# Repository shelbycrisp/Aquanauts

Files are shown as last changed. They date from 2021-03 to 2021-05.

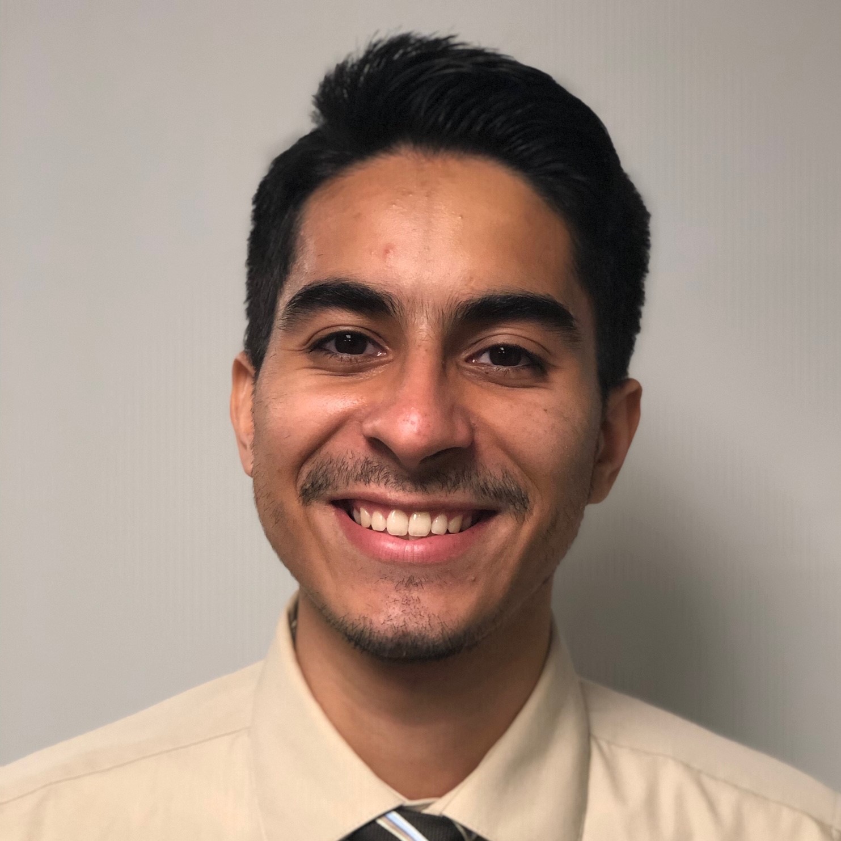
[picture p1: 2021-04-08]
website/ruben-headshot.JPG

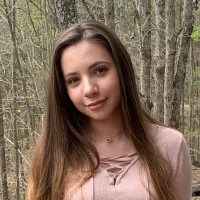
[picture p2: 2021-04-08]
website/shayna-headshot.jpg

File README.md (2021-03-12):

# Aquanauts
## Summary

The Exxon Valdez oil spill of 1989 is generally considered to have the largest environmental impact of any oil spill to date. Ocean Scientists at Prince William Sound have been using an underwater profiler to monitor environmental factors. The platform has an anchor that holds it at a specified depth. The platform goes to the surface of the water once a day to transmit a signal that it is still alive. The data collected on ocean life and ocean currents is not transmitted and must be retrieved by scientists. The collected data gives scientists information on how the location and its inhabitants are recovering. There are multiple ways this platform can be improved and updated. Currently, someone must retrieve the platform every few weeks in order to charge the battery and extract data. Over time the battery life has decreased, further increasing the maintenance required. If this maintenance could be decreased that would be a great improvement for the platform. Currently, it is very difficult and expensive to replace the battery. A battery that can be serviced by the scientists themselves would be ideal. The platform has many sensors on board to detect ocean life such as plankton. The current solution to classifying plankton is through the use of machine learning. However, there is room for improvement in this component. There is a weather buoy nearby that could potentially be used to install components on for communication with the platform. Our team is identifying which features/issues to focus our project on.

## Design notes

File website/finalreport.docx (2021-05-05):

Prince William Sound Profiler

ECE 4873 Senior Design Project

Aquanauts

Dr. Mick West

Dr. Robert Campbell (if applicable)

Shayna Seidel, EE, sseidel7, sseidel7@gatech.edu

Jim O’Donnell, CmpE, jodonnell3, jodonnell3@gatech.edu

Shelby Crisp, CmpE, scrisp3, scrisp3@gatech.edu

Jason Lee, EE, slee3117, slee3117@gatech.edu

Ruben Quiros, CmpE, rquiros6, rquiros6@gatech.edu

Timothy Pierce, EE, tpierce31, timrpierce31@gatech.edu

Table of Contents

Executive Summary …………………………………………………………………... 3

1. Introduction ……………………………………………………………………….. 5
2. Project Description and Goals ……………………………………………………. 7
3. Technical Specification ……………………………………………………………. 9
4. Design Approach and Details …………………………………………………….. 10
  4.1 Design Concept Ideation, Constraints, Alternatives, and Tradeoffs …………. 10
  4.2 Preliminary Concept Selection and Justification …………………………….. 12
  4.3 Engineering Analysis and Experiments …………………………………….... 17
  4.4 Codes and Standards …………………………………………………………. 17
5. Project Demonstration …………………………………………………………….. 19
6. Schedule, Tasks, and Milestones ………………………………………………… 23
7. Marketing and Cost Analysis …………………………………………………….. 25
  7.1 Marketing Analysis …………………………………………………………... 25
  7.2 Cost Analysis …………………………………………………………………. 26
8. Current Status …………………………………………………………………….. 27
9. Leadership Roles ………………………………………………………………….. 28
10. References …………………………………………………………………………. 29

Appendix ……………………………………………………………………………. 31

Executive Summary

The goal of this project was to design a new communications system for an existing underwater profiler. This allows a data-collecting profiler in the Prince William Sound to send the collected data to researchers. The current transfer of information necessitates a biweekly data transfer on site of the profiler, which is 4 hours offshore in the Prince William Sound. With the newly designed communications module, data will be transferred once every 12 hours without the need for onsite download. This module needs to surface and communicate wirelessly to the shore in an environment with few options for long range transfer of data. The profiler currently uses low bandwidth cellular data to send minimal information every 12 hours. The new system should not take up too much battery life, and should include an interface between existing sensors that are necessary to surface in the profiler. The total cost for this project was $354.85.

Nomenclature

AMP: Autonomous Moored Profiler

BOM: Bill of Materials

CmpE: Computer Engineer

EE: Electrical Engineer

PCB: Printed Circuit Board

PWS: Prince William Sound

Prince William Sound Profiler Communication Module

1. Introduction

In the aftermath of the 1989 Exxon Valdez oil spill in Prince William Sound, an Autonomous Moored Profiler (AMP) has been used (since 2013) to collect data on PWS’s environmental recovery [1]. Although originally manufactured by Sea-Bird Scientific, the profiler is no longer in production. The current profiler in PWS continues to monitor the environmental recovery of PWS, but requires numerous updates and improvements. This is why the Aquanauts team created a data transmission system for the profiler in Prince William Sound. This system is able to send data from the profiler sensors to the ocean scientists and give the scientists the flexibility to individually control sensors. This functionality will give scientists more information on a regular basis. The total cost for this project was $354.85.

Currently, scientists must visit the profiler approximately every two weeks to charge the battery and manually collect data. Making frequent maintenance trips to the profiler is inefficient, and can become delayed or even dangerous due to weather conditions. Remote access to sensor data would greatly enhance the profiler's usage. Data transmission would require using the nearby 3G cell tower to transmit data to the ocean scientists so they could access it without making a trip to the profiler.

The current system has all the sensors on a single relay system such that sensors cannot be individually controlled. Certain sensors cannot collect data as the profiler travels downward, so all sensors are off during this time. A new relay system that can control sensors individually would allow more flexibility for data collection and increase the amount of data collected.

This design involved connecting all sensors to the new switching board and a centralized microcontroller, and designing a method for the system to transmit data when at the surface. There were multiple constraints that had to be taken into account for this design. Due to the nature of the profiler, designs must withstand the extreme pressure, temperature, and storms of PWS. The system must also fit inside a 3.937 inch diameter capsule. These requirements were factored into the design. Once the design was complete, a combination of simulations and physical tests were conducted to demonstrate the module’s capabilities. The verification was a video and presentation used at the Spring 2021 Senior Design Expo. The rest of this report will go into greater detail on the specifics of designing and validating this system.

2. Project Description, Customer Requirements, and Goals

The Aquanauts team proposed a new sensor module in addition to the overall profiler assembly to address three of the customer’s main requirements: improved data transfer from the profiler’s remote location, extended battery life of the overall profiler, and updated central data storage. The new module addresses these requirements in the following ways:

1. Revamp the method of communication to improve data transfer volume and speed by utilizing the available 3G/4G cell tower nearby.
2. Provide physical infrastructure and software capability to turn individual sensors on and off on a schedule, thus saving critical battery life.
3. Provide a modern microprocessor and data storage unit for aggregation and processing of data, replacing the outdated and no longer produced Persistor module.

Success and stakeholder acceptance will be measured by benchmarking performance of the new module versus current-state performance. Notably, current-state data transfer is every 10th data point amounting to around 200kb of data, with the majority of communication representing an “alive” signal that indicates whether the profiler is still functioning. Battery life is estimated between 3 weeks and 1 month, with the majority of power drain resulting from the anchoring winch. The project’s internal stakeholder is Dr. West, while the external stakeholder is Dr. Campbell and his team in Alaska.

Table 1. Stakeholder 2x2

Internal Stakeholders | External Stakeholders
Dr. West, Aquanauts | Dr. Campbell

Constraints are minimal. The intent of the long-term project with the research team is to design a new profiler as the existing profiler is no longer manufactured. The Aquanauts’ goal is to provide an ideal sensor and communication subsystem to address the research team’s requirements, rather than consider integration with other existing systems. Considerations include data transfer rate, low power consumption, environmental survivability of the components in terms of temperature and pressure in a very cold underwater environment, and appropriate storage capacity to accommodate profiling data.

Table 2. QFD Chart

| Long-Range Communication | Centralized Data Storage and Processing | Extended Battery Life | Extended Profiling Capability | Total
Form Factor | 2 | 4 | 10 | 10 | 26
Power Consumption | 4 | 4 | 10 | 7 | 25
Environmental Conditions | 10 | 10 | 2 | 2 | 24
Total | 16 | 18 | 22 | 19

3. Technical Specifications

Table 3. Technical Specifications

Specification | Min | Max
Functional Temperature | -5 C | 30 C
Functional Depth | N/A | 60m
Total Power Consumption for Sensors | 12 V DC, 480 mA (** Missing min amp info for SBE 16plus V2) | 12 V DC, 1.1 A (**Missing max amp info for SBE 16plus V2)
Communication Range (Approx) | 8000m (Nearest cell tower, approximately 5 mi.) | N/A
Communication Protocols | 3G, 4G, FTP/SFTP

The specifications listed in Table 3 indicate the foundational requirements of the integrated system, including functional temperature, depth, power consumption, communication range, and communication frequency. All defined sections are equally important as they encompass environmental considerations for the remote underwater locale, power consumption considerations in terms of saving critical battery life, and communications requirements for improved data transfer. The minimum power consumption is determined from the highest minimum operating voltage of all sensors, and maximum power consumption is determined from the lowest maximum operating voltage of all sensors. Minimum communication range is an approximation based on the operating depth of the profiler to a theoretical buoy containing additional communication equipment, and maximum communication range is from the profiler’s location to the nearest cell tower 5 miles (~8000 meters) away. 3G and 4G are the fastest available communication protocols using the nearby cellular tower.

4. Design Approach and Details
  4.1 Design Concept Ideation, Constraints, Alternatives, and Tradeoffs

The current design concept for this project is to have a central processor which will interface between the different sensors used by the profiler. The processor will store sensor data in a central place as well as interface with a cellular communication module to send the data out while profiling.

4.1.1 Power Switching Functionality

In order to have the capability to control individual sensors, a power switching system needed to be designed. The system currently used in PWS has all the sensors on a single relay so they are all turned on and off together. To control sensors separately, they must each have their own power switch.

Using optocouplers for each sensor was initially considered, but no optocouplers with a high enough current rating and low enough price were found. Next, solid state relays were considered for their long term reliability, but similarly to the high current optocouplers, solid state relays are expensive. Finally, MOSFETs were considered because all of the sensors use DC power. MOSFETs were chosen for their ease of implementation as well as their low price. Each sensor has a corresponding MOSFET that when conducting, connects the ground lead of the sensor to ground and allows the sensor to receive the necessary voltage and draw the needed current.

Table 4. Switching Board Tradeoffs

Tradeoffs for Power Switching Board
Pros | - Individual control of sensors
Cons | - A new board had to be designed - Components for board had to be purchased

4.1.2 Data Transmission

Data transmission is a main focus for this project. Different concepts were considered, including satellite transmission for data, cellular telemetry and radio transmission. Cellular data is what is currently utilized for transmitting information from the profiler to shore. Using cellular data made the most sense for application of this project. Since cellular data was already being utilized, it was more ideal for use in testing as opposed to radio transmission and satellite transmission. There is a cellular tower near the sound that can support 3G/4G communications.

While cellular data is useful to utilize, the constraint of inability to send data without surfacing still comes into play. Satellites would require a buoy and therefore a signal would persist even under harsher conditions. However, upon further inspection, satellites were beyond the budget of this project and not many companies support satellite communication at such a remote location. Viasat, one of the larger and more affordable companies to offer satellite transmission, doesn’t immediately offer transmission to the sound [2]. Radio transmission is another option to explore, but would require testing and setup in the sound that would have been hard to reproduce offsite.

Table 5. Cellular Data Tradeoffs

Tradeoffs for Cellular data usage
Pros | - In use currently - Easier to test
Cons | - Doesn’t work if the module doesn’t surface - May have lower speeds than other alternatives

4.1.3 Centralized Sensors

In order to successfully collect and store data as well as control the sensors and communications module, a central processor was necessary. The one already in use, a Persistor, is no longer being produced. Multiple microcontrollers were considered such as Arduino Mega and multiple Raspberry Pi models. Ultimately a Raspberry Pi model 3B was selected. This model of Raspberry Pi uses the least power while offering Linux compatibility to support well-known communication protocols like FTP/SFTP/SCP as well as the Sixfab Cellular Kit.

This PCB and microcontroller must fit inside the capsule and be able to function at low temperatures and high pressure in an underwater environment.

An alternative would be to keep the current processor. Since it is no longer being produced and uses outdated software, it would be close to impossible to test the integration of sensors and communication modules. If any damage were to occur with the current processor, it would be harder to replace than something like an Arduino or Raspberry Pi which are still in production.

Table 6. Updating Central Storage Tradeoffs

Tradeoffs for Updating central storage
Pros | - Old processor no longer in production - Can update software - Compatible with cellular kit
Cons | - Added cost - Old processor still working and in use

  4.2 Preliminary Concept Selection and Justification

4.2.1 Power Switching Functionality

After discussing the power requirements with Dr. West and Dr. Campbell, the Aquanauts decided to design a PCB that allowed for the sensors to be turned on and off individually using MOSFETs. Currently, the profiler lacks individual sensor power control and all sensors must be turned on at the same time. Individual sensor power control will allow the profiler to collect data on its descent. The ability to turn on only the needed sensors will conserve battery life.

The selected power switches for sensor control are FQP30N06L power MOSFETs. These power MOSFETs were chosen for their high power dissipation capabilities and their ease of implementation. The chosen MOSFETs are capable of dissipating 79W of power which far exceeds the power draw of any of the onboard sensors. The maximum power draw of any of the individual sensors is 11.25W which is low enough to not require the use of heat sinks on the MOSFETs.

To convert the voltage to usable DC levels for both the sensors and the Raspberry Pi, two DC-DC Buck converters were used to buck the voltage from the onboard 30V 1.5kWHr battery. All four sensors currently on the profiler have voltage ranges that include 12V so this was the selected voltage for conversion. A Mean Well 18-36V to 12V power converter was used that is capable of outputting 30W - significantly more than the maximum power draw of all four sensors. To buck the voltage to usable levels for the Raspberry Pi, a Traco Power 12W, 5.1V output buck converter was used.

There are currently four sensors on the profiler, but a total of six MOSFET switches were added to allow more sensors to be added in the future. To control the MOSFETs, a separate GPIO pin from the Raspberry Pi was connected to the gate of each MOSFET. The GPIO pin from the Raspberry Pi was set to 3.3V to trigger the MOSFET and supply the connected sensor with 12V. To protect the sensors in case of a voltage or current spike, a fuse specified for the power requirements of each sensor was added.

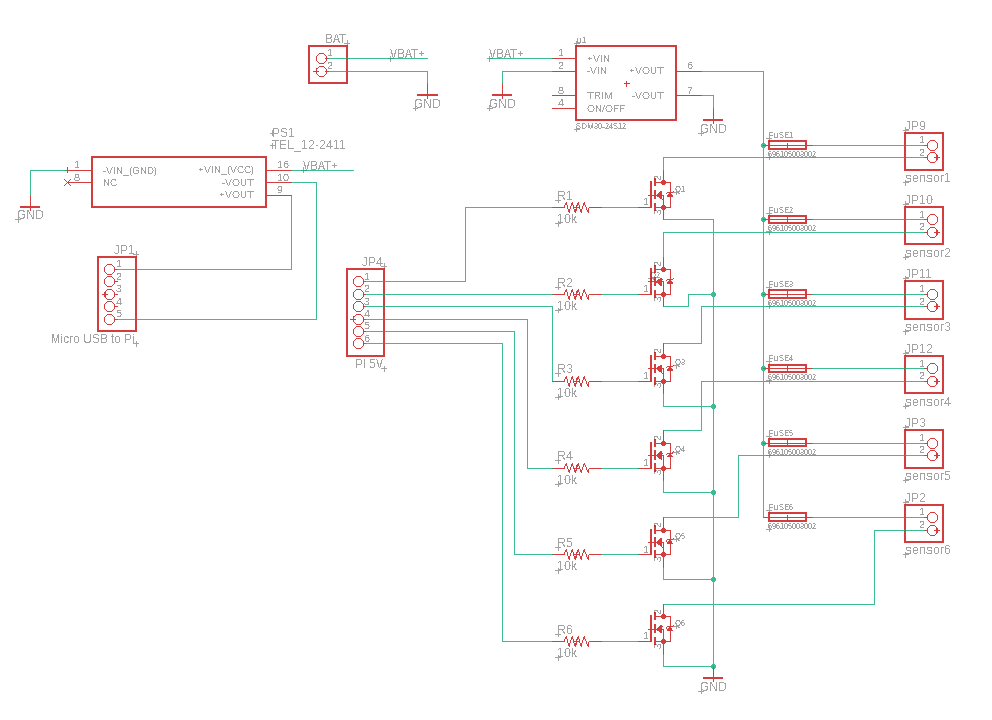
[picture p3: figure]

Figure 1. Eagle schematic showing the layout for the MOSFET sensor switching board

Once the schematic was completed, the PCB was designed with several constraints in mind. Each trace on the PCB is rated for 2.5A which is greater than the highest current draw of a sensor by more than a factor of 1.5. The PCB was also designed to fit in a vacuum sealed tube suitable for keeping electronics dry under water. The diameter of the tube is 100mm or 3.937in and the dimensions of the PCB are 3.5 inches by 3.9 inches. When creating the layout of the PCB, thermal and ease of use considerations were taken into account. The components that generate the most heat, the DC-DC converters and the MOSFETs, were spaced out as much as possible while also keeping the PCB within size constraints. Additionally, the MOSFET, fuse, resistor, and pin header for each individual sensor were grouped together in order to make identifying blown fuses and their corresponding sensor easier.

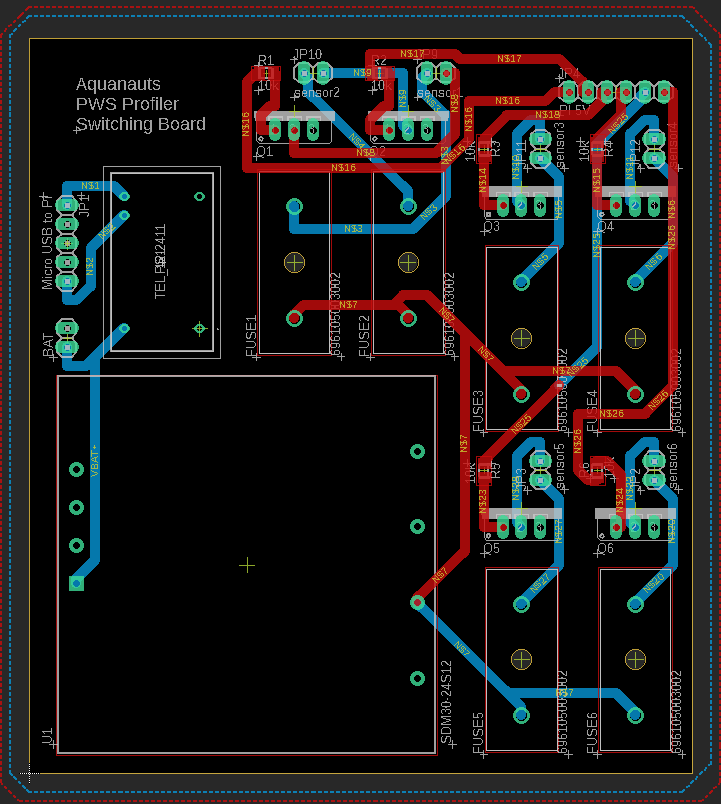
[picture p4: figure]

Figure 2. The final MOSFET sensor switching board PCB layout. The dimensions of the board are 3.9 inches (from top to bottom) by 3.5 inches (from left to right)

4.2.2 Centralized Sensors

Currently, data from the sensors is stored in a central location using ASCII text. The main storage unit is a Persistor which is outdated and no longer produced. A new microcontroller must be chosen to accommodate the sensors on the module, cellular data transmission, expandable memory, and ease of programming. The sensors the microcontroller needs to interface with are: SBE 49 FastCAT CTD Sensor, RBR Brevio, Seabird Eco FLNTU, SBE 63 Optical Dissolved Oxygen Sensor, Aanderaa Oxygen Optode, and Seabird SUNA V2 Nitrate Sensor. A Raspberry Pi 3B was used to replace the Persistor. This was best suited for this project because it has many pins to accommodate the sensors, expandable pin modules can be added if needed, and there are multiple kits already developed for using cell data with a Raspberry Pi. Raspberry Pi’s run using a limited version of Ubuntu. This would give our team easy access to a multitude of preexisting data transmission commands. The Pi 3B can run these commands without the excessive power draw of the Pi 4.

4.2.3 Data Transmission

When the module is at the surface, data from the sensors will be transmitted. Currently when the profiler surfaces, a nearby 3G cell tower is used to send minimal information. Due to availability and cost, the Aquanauts plan is to continue to use this cell tower for the increased data transmission. The Aquanauts have selected the Sixfab 4G LTE Cell Hat. This kit is specifically designed to interface with 4G cellular towers which are currently being utilized in the sound. This kit is comprehensive, which was an attractive feature for our team in testing, but in the future a more whittled down version could be used. While 5G was considered, the 4G cellular tower was just installed in the Prince William Sound, and the likelihood that 4G would become obsolete any time soon is unlikely.

  4.3 Engineering Analyses and Experiment

The Aquanauts team performed simulations for both hardware and software for experiments on our design. The three Computer Engineers were tasked with simulating the system in software, with programs and libraries that operate on the final product. When the three Electrical Engineers designed and fabricated the PCB, they were in charge of performing tests on the hardware to make sure it could safely operate under the required power conditions. Power consumption was monitored to determine how much power the overall module would consume.

In the following phase, the software and hardware teams were able to test the overall system. The team performed experiments to make sure that the processing unit was able to send data through the new communication system. This involved the use of real data that Dr. Campbell has collected. Unfortunately, the team did not have access to neither the battery nor the sensors. As a result, a 2 W resistor was used to simulate the sensor, and a DC power supply was used to simulate the battery. This proved that the current electronics worked with a new communication system and a centralized data processing unit.

  4.4 Codes and Standards

The relevant codes and standards include the following:

- IMT-2000: Offers the capability of providing value-added services and applications for frequencies between 400 MHz and 3 GHz [6].
  - Adds compatibility feature with existing systems such as 2G
  - Makes 3G systems affordable
- 802.15.4-2020 - IEEE Standard for Low-Rate Wireless Networks: The standard provides for ultra low complexity, ultra low cost, ultra low power consumption, and low data rate wireless connectivity among inexpensive devices, especially targeting the communications requirements of what is now commonly referred to as the Internet of Things [7].
5. Project Demonstration

To validate the specifications of the Prince William Sound Profiler communication system and sensor switching board, a series of both software and hardware tests were performed. Testing the communication system used the Raspberry Pi 3b, the Raspberry Pi cellular kit, the Samsung Evo SSD, and the custom printed circuit board. A DC-DC buck converter on the PCB was used to lower the battery-level voltages to 5.1V to power the Raspberry Pi. The Raspberry Pi was connected to the PCB, and the SSD and Sixfab cellular kit were connected to the Raspberry Pi. Using a remote FTP server hosted off campus, the communication module was tested by executing a shell script on the Raspberry Pi, which sent sample data files to the FTP server through a wireless connection.

For the validation of the sensor switching system on the custom PCB, both software simulations and hardware tests were performed. First, a single MOSFET switching circuit was simulated using LTSpice to verify that the chosen design could power the sensor by providing 12V and then turn off the sensor by providing 0V. To simulate the sensor, a 75Ω, 2W resistor was used to draw a current of about 160mA.

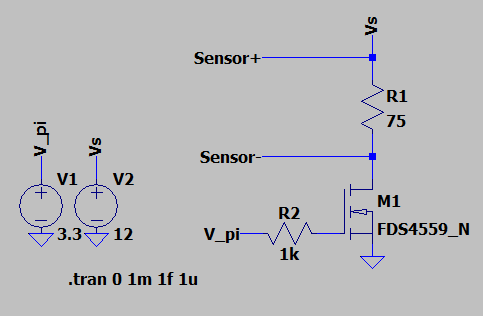
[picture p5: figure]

Figure 3. LTSpice schematic for a single MOSFET sensor switch when the Raspberry Pi sends a 3.3V signal to turn the sensor on

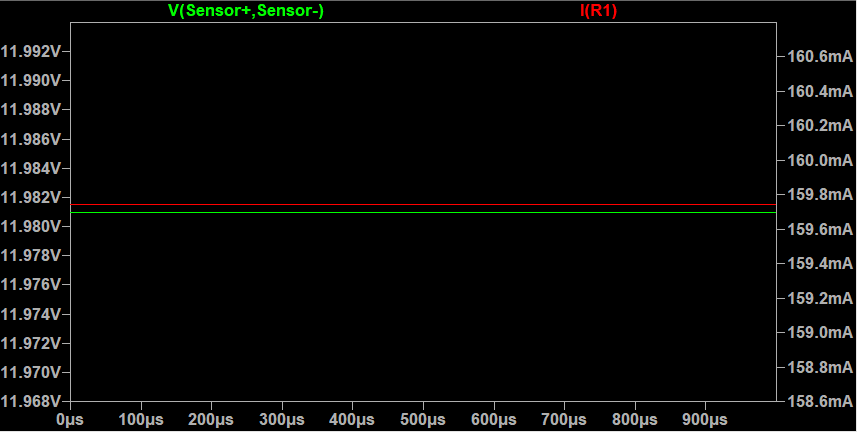
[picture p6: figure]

Figure 4. LTSpice transient simulation results showing 12V and 160mA being supplied to the 75Ω resistor simulating a sensor

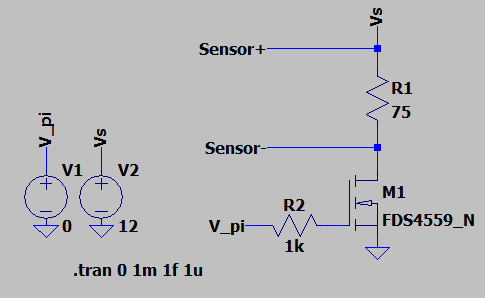
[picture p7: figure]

Figure 5. LTSpice schematic for a single MOSFET sensor switch when the Raspberry Pi sends a 0V signal to turn the sensor off

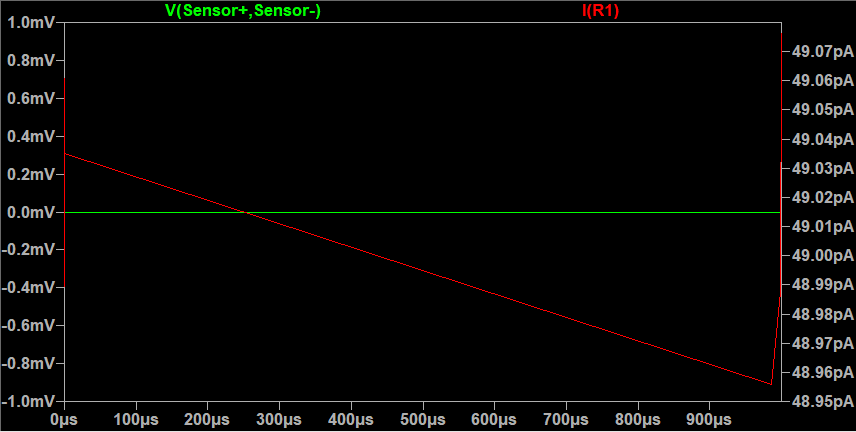
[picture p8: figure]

Figure 6. LTSpice transient simulation results showing 0V and nearly 0mA being supplied to the 75Ω resistor simulating a sensor

Once the custom PCB with the sensor switching system was complete, hardware tests were performed to verify that the switching system worked as intended. The Raspberry Pi was hooked up to the PCB and a 75Ω, 2W resistor was wired to the output of the MOSFET switching system. The voltage across the resistor and the current through the resistor were measured using a digital multimeter. When the Raspberry Pi supplied 3.3V to the gate of the MOSFET, the voltage across the resistor was 12V and the current through the resistor was 160mA. When the Raspberry Pi supplied 0V to the gate of the MOSFET, the voltage across the resistor was reduced to 0V and the current across the resistor was reduced to 0mA, effectively turning the “sensor” off.

When the design aspect of the project was complete, results were prepared and presented at the Spring 2021 Senior Design Capstone Expo. A poster was created to show an overview of the system that was designed, and a project video was created to present motivations for this project and demonstrate the system.

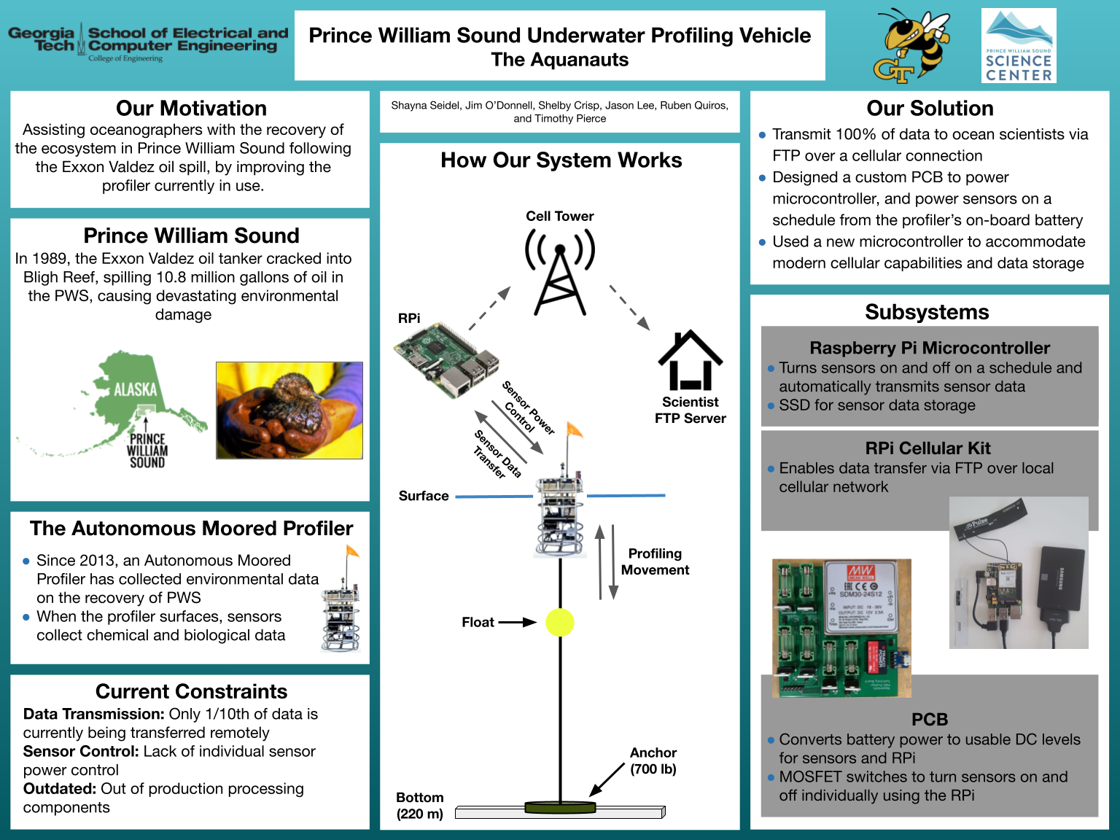
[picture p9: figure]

Figure 7. Senior Design Capstone Expo Poster with background information of the project and an overview of the designed system

6. Schedule, Tasks, and Milestones:

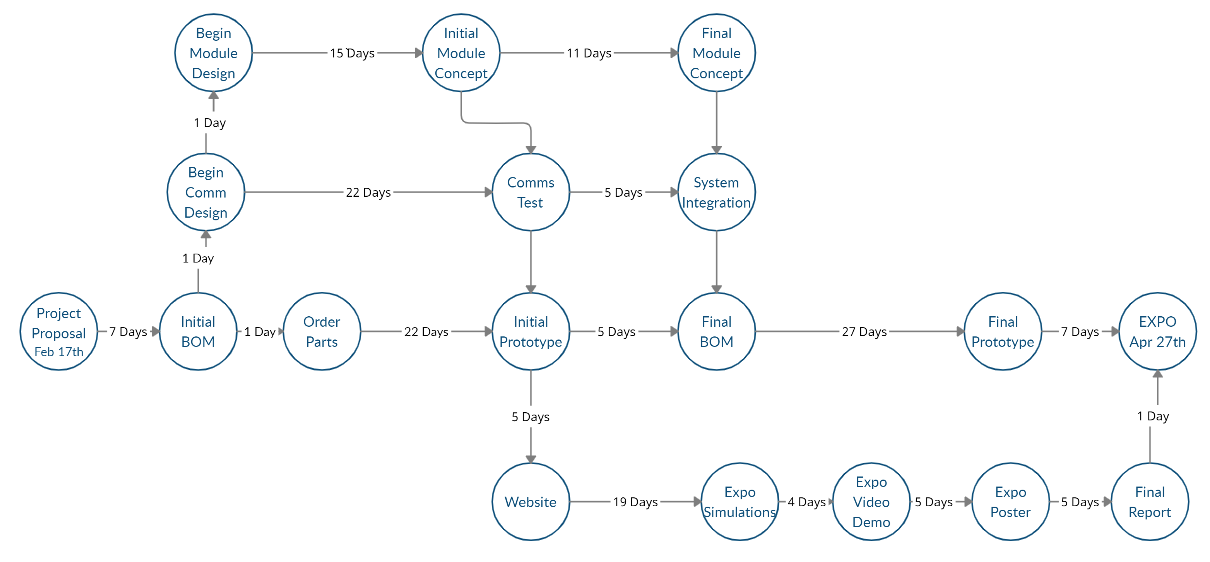
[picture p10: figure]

Figure 8. PERT Chart showing the expected timeline for module development

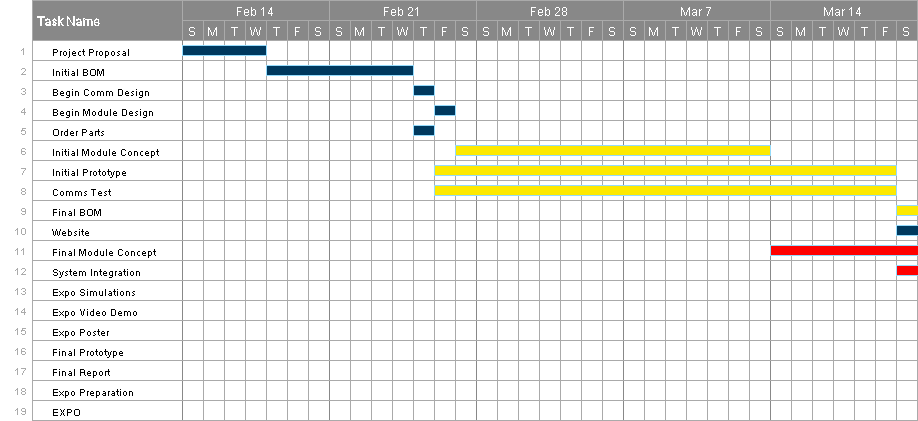
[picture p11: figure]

Figure 9. Gantt chart for February 14th to March 20th showing a timeline of project phases and their estimated difficulty. Purple indicates low difficulty, yellow indicates medium difficulty, and red indicates high difficulty.

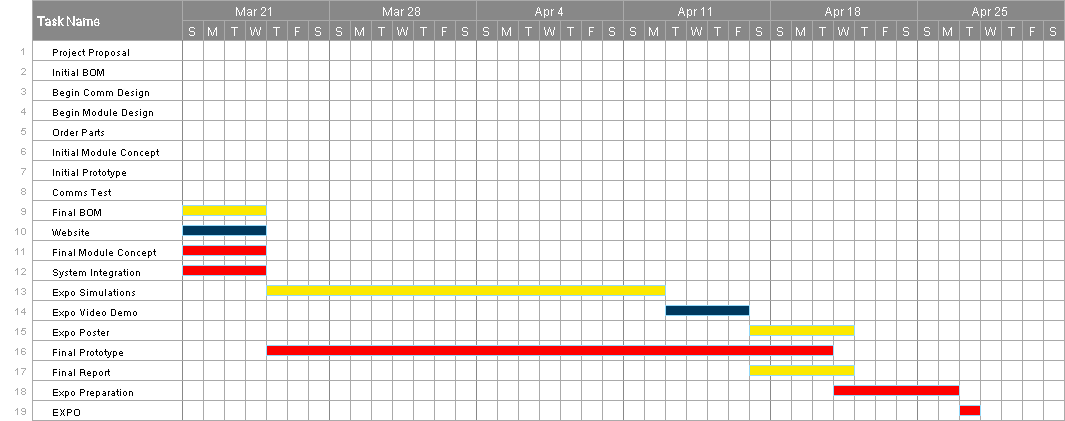
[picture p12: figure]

Figure 10. Gantt chart for March 21st to April 27th showing a timeline of project phases and their estimated difficulty. Purple indicates low difficulty, yellow indicates medium difficulty, and red indicates high difficulty.

At the start of the project, the chance of successful project completion by April 27th was determined to be 95%. The project utilized pre existing technology and did not rely on any significant technological breakthroughs. The completion of the project did not directly follow the outlined timeline in the PERT chart and Gantt charts. Much more time was dedicated to initial product research and design. Because more time was devoted to designing the system for this project, less time was needed for the final prototype and integration of the system. Additionally, significantly less time was needed for expo preparation. After a successful Senior Design Capstone Expo, the goal was met and the project was officially completed by the deadline.

7. Marketing and Cost Analysis
  7.1 Marketing Analysis

The proposed communication module is a newly designed long range wireless communication unit that will be an addition to a Sea Bird Thetis profiler currently deployed in the Prince William Sound. What is currently in use for external communications is an RS-232 100 Mbps serial to IP ethernet device. This sends a signal when the profiler itself surfaces.

There are some products that boast wireless communications without the necessity to leave the water. DSPComm has a line of underwater acoustic modems [8]. They are manufactured to be used underwater and can transmit a signal up to 3km away. Our product does not need to have such a long underwater range, as it can surface to transmit.

Another similar product on the market is the MarineLabs CoastScout. This long range communication buoy is a self-contained and self-powered buoy that is capable of transmitting 5MB wirelessly. The CoastScout is its own data collection device that collects weather and water data and sends it to a remote server. Our device differs from the CoastScout because instead of collecting its own data and sending it, it will be sending data that was collected by the underwater Thetis profiler. Additionally, the communication module will rely on power from the Thetis profiler battery instead of solar power.

  7.2 Cost Analysis

Table 7. Costs

Part | Manufacturer | Retailer | Price per Item | Quantity | Part Total
Raspberry Pi 3B | Raspberry Pi | Amazon | 37.99 | 1 | 37.99
Raspberry Pi 4G/LTE Cellular Modem Kit | Sixfab | Sixfab | 109 | 1 | 109
Sixfab Connect Sim | Sixfab | Sixfab | 2 | 1 | 2
SAMSUNG PRO Plus SDHC Full Size SD Card 32GB | Samsung | Amazon | 9.99 | 1 | 9.99
MKR SD PROTO SHIELD | Arduino | Arduino | 13.8 | 1 | 13.8
USB 3.0 SATA III Hard Drive Adapter Cable, SATA to USB Adapter Cable | SKL Tech | Amazon | 7.99 | 1 | 7.99
SAMSUNG 870 EVO 250GB 2.5 Inch SATA III Internal SSD | Samsung | Amazon | 39.99 | 1 | 39.99
30 W DC/DC Converter | Mean Well USA | Digi-Key | 26.71 | 1 | 26.71
FQP30N06L | ON Semiconductor | Digi-Key | 1.22 | 6 | 7.32
USB to Serial RS232 Adapter | SIIG | Amazon | 49.85 | 1 | 49.85
12 W DC/DC Converter | Traco Power | Digi-Key | 28 | 1 | 28
PCB | JLC PCB | JLC PCB | 14.8 | 1 | 14.8
500 mA Fuse | Bel Fuse Inc | Digi-Key | 0.234 | 5 | 1.17
1A Fuse | Bel Fuse Inc | Digi-Key | 0.224 | 5 | 1.12
5x20 mm Fuse Holder | Würth Elektronik | Digi-Key | 0.64 | 8 | 5.12

Total

354.85

8. Current Status

The overall task of this project was to create a new communication system for the underwater profiler, which will be a major upgrade to the original system. Sub-tasks are listed below:

a. Designing a subsystem that collects data from all sensors on the profiler - COMPLETE
  i. Design and manufacture a PCB to control sensors individually and power the microcontroller - COMPLETE
b. Designing a subsystem that will send the data to the research facility over a wireless connection - NEARLY COMPLETE
  i. Testing the ability to send files over WiFi - COMPLETE
  ii. Testing the ability to send files over a cellular connection - INCOMPLETE.
- Due to time constraints at the end of the semester and troubleshooting issues, we were unable to complete testing of the AT command set with our cellular HAT. We have included as much information as we were able to gather, and the process is detailed nearly in full in the User Manual. This would be a good place for a future team to continue research and testing.
c. Create a full BOM - COMPLETE
  i. Order parts - COMPLETE
d. Project proposal and presentation - COMPLETE
9. Leadership Roles
a. Group Leader: Jim O’Donnell
- Main speaker and scheduling coordinator
b. Expo Coordinator: Shayna Seidel
- In charge of making sure the team is aware of all requirements for the expo
c. Financial Advisor: Seungju Jason Lee
- Responsible for keeping track of receipts and handling reimbursements
d. Webmaster: Ruben Quiros
- Responsible for managing the team’s website
e. Documentation Coordinator: Timothy Pierce
- In charge of maintaining and submitting documentation on behalf of the group
f. Tech lead: Shelby Crisp
- Host and manager of the git repository
10. References
1. R. W. Campbell, P. L. Roberts, and J. Jaffe, “Prince William Sound Plankton Camera: a profiling in situ observatory of plankton and particulates,” OUP Academic, 24-Mar-2020. [Online]. Available: https://academic.oup.com/icesjms/article/77/4/1440/5811106. [Accessed: 17-Feb-2021].
2. Admin, “How it Works: The technology behind satellite internet,” Viasat.com. [Online]. Available: https://www.viasat.com/about/newsroom/blog/how-it-works-the-technology-behind-satellite-internet/. [Accessed: 18-Feb-2021].
3. S.-B. S. USA, “Thetis Autonomous Moored Profiler Datasheet,” Sea-Bird Scientific. [Online]. Available: https://www.seabird.com/systems/thetis-profiler/family-downloads?productCategoryId=54627869948. [Accessed: 17-Feb-2021].
4. ARDUINO SIM - MKR GSM 1400 Cellular Kit. [Online]. Available: https://store.arduino.cc/usa/sim-bundle. [Accessed: 17-Feb-2021].
5. H. H. A. K. A. www.crazyhamster.co.uk, IP Ratings Explained - know your enclosure Ingress Protection ratings. [Online]. Available: https://www.enclosurecompany.com/ip-ratings-explained.php. [Accessed: 17-Feb-2021].`
6. “About mobile technology and IMT-2000,” International Telecommunication Union. [Online]. Available: https://www.itu.int/osg/spu/imt-2000/technology.html. [Accessed: 17-Feb-2021].
7. “802.15.4-2020 - IEEE Standard for Low-Rate Wireless Networks,” IEEE Xplore. [Online]. Available: https://ieeexplore.ieee.org/document/9144691/metrics#metrics. [Accessed: 18-Feb-2021].
8. “Products,” Underwater Wireless Modem and Communication Devices, 05-Feb-2021. [Online]. Available: http://www.dspcommgen2.com/products/. [Accessed: 18-Feb-2021].
9. Xylem, Aanderaa Oxygen Optode 4531. Xylem, Bergen, Norway, 2020. Datasheet. https://www.aanderaa.com/productsdetail.php?Oxygen-Optodes-2
10. Xylem, Aanderaa Oxygen Optode 4835. Xylem, Bergen, Norway, 2020. Datasheet. https://www.aanderaa.com/productsdetail.php?Oxygen-Optodes-2
11. RBR, RBRBrevio C.T.D. RBR, Ottawa, Ontario, 2019. Datasheet. https://rbr-global.com/products/standard-loggers/rbrbrevio
12. Seabird, ECO FLbb Fluorometer and Scattering Meter. Seabird, Bellevue, WA, 2021. Datasheet. https://www.seabird.com/combination-sensors/eco-flntu/family?productCategoryId=54758054352
13. Seabird, SBE 49 FastCAT CTD Sensor. Seabird, Bellevue, WA, 2015. Datasheet. https://www.seabird.com/profiling/sbe-49-fastcat-ctd-sensor/family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
14. Seabird, SBE 63 Optical Dissolved Oxygen Sensor. Seabird, Bellevue, WA, 2014. Datasheet. https://www.seabird.com/oxygen-sensors/sbe-63-optical-dissolved-oxygen-sensor/family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
15. Seabird, SUNA V2 UV Nitrate Sensor. Seabird, Bellevue, WA, 2017. Datasheet. https://www.seabird.com/nutrient-sensors/suna-v2-nitrate-sensor/family?productCategoryId=54627869922

Appendix

Sensors | Min Voltage | Max Voltage | Min Current (mA) | Max Current (mA)
SBE 16plus V2 | 9 | 28 | N/A | N/A
SBE 43 | 6.5 | 24 | 2.5 | 9.23
SUNA Nitrate Sensor | 8 | 18 | 416.67 | 937.5
Echo Fluorometer | 7 | 15 | 60 | 140

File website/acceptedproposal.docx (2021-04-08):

Prince William Sound Profiler Communication Module

ECE 4873 Senior Design Project

Aquanauts

Dr. Mick West

Dr. Robert Campbell (if applicable)

Shayna Seidel, EE, sseidel7, sseidel7@gatech.edu

Jim O’Donnell, CmpE, jodonnell3, jodonnell3@gatech.edu

Shelby Crisp, CmpE, scrisp3, scrisp3@gatech.edu

Jason Lee, EE, slee3117, slee3117@gatech.edu

Ruben Quiros, CmpE, rquiros6, rquiros6@gatech.edu

Timothy Pierce, EE, tpierce31, timrpierce31@gatech.edu

Submitted

2/17/21

Table of Contents

Executive Summary 3

1. Introduction ……………………………………………………………………….. 5
2. Project Description and Goals ……………………………………………………. 7
3. Technical Specification ……………………………………………………………. 9
4. Design Approach and Details …………………………………………………….. 10
  4.1 Design Approach ……………………………………………………………... 10
  4.2 Codes and Standards …………………………………………………………. 15
5. Project Demonstration …………………………………………………………….. 17
6. Schedule, Tasks, and Milestones ………………………………………………… 18
7. Marketing and Cost Analysis …………………………………………………….. 20
  7.1 Marketing Analysis …………………………………………………………... 20
  7.2 Cost Analysis …………………………………………………………………. 20
8. Current Status …………………………………………………………………….. 22
9. Leadership Roles ………………………………………………………………….. 23
10. References …………………………………………………………………………. 24

Appendix ……………………………………………………………………………. 26

Executive Summary

The goal of this project is to design a new communications module for an existing underwater profiler. This module will be able to send data from a data-collecting profiler in the Prince William Sound to the researchers working on it. The current transfer of information necessitates a biweekly data transfer on site of the profiler, which is 4 hours offshore in the Prince William Sound. By designing a new communications module, data will be transferred once every 24 hours without the need for onsite download. This module will need to surface in the sound and communicate wirelessly to shore in an environment with few options for long range transfer of data. The profiler currently uses low bandwidth cellular data to send minimal information every 24 hours. The added module shouldn’t take up too much battery life, and should include an interface between existing sensors that are necessary to surface in the profiler. The expected cost is $183.78.

Nomenclature

AMP: Autonomous Moored Profiler

BOM: Bill of Materials

CmpE: Computer Engineer

EE: Electrical Engineer

PWS: Prince William Sound

Prince William Sound Profiler Communication Module

1. Introduction

In the aftermath of the 1989 Exxon Valdez oil spill in Prince William Sound, an Autonomous Moored Profiler (AMP) has been used (since 2013) to collect data on PWS’s environmental recovery [1]. Although originally manufactured by Sea-Bird Scientific, the profiler is no longer available. The current profiler in PWS continues to monitor the environmental recovery of PWS but requires numerous updates and improvements. This is why the Aquanauts team is requesting $400 of funding to create a data transmission module for a profiler in Prince William Sound. This module will be able to surface and send data from the profiler sensors to the ocean scientists. This functionality will save energy thus reducing the maintenance frequency while giving scientists more information on a regular basis. The current cost estimate for parts for this module is $183.78, however, the total project will cost more when PCB printing and components that are unaccounted for are taken into account.

Currently, scientists must visit the profiler approximately every two weeks to charge the battery. These maintenance visits are when data from the sensors is collected. Making frequent maintenance trips to the profiler is inefficient, and can become delayed or even dangerous due to weather conditions. Saving battery life and accessing sensor data remotely would greatly enhance the profiler's usage. Developing a smaller module to surface, as opposed to the entire large platform, would save battery life and decrease maintenance visits. This module would also use the nearby 3G cell tower to transmit data to the ocean scientists so they could access it without making a trip to the profiler.

This module will require a separate smaller winch to ascend to the surface. However, the Aquanaut’s focus is on the module itself and mainly its software and electrical hardware components. This will involve connecting all sensors to the module and a centralized microcontroller, and designing a method for the module to transmit data when at the surface. There are multiple constraints that must be taken into account for this design. Due to the nature of the profiler, designs must withstand the water, pressure, temperature, and harsh storms of PWS. These requirements will be factored into the design. Once design is complete, a combination of simulations and physical tests will be conducted to demonstrate the module’s capabilities. The verification will be videos for use at the Spring 2021 Senior Design Expo. The rest of this report will go into greater detail on the specifics of designing and validating this module.

2. Project Description, Customer Requirements, and Goals

The Aquanauts team proposes a new sensor module in addition to the overall profiler assembly to address four of the customer’s main requirements: improved data transfer from the profiler’s remote location, extended battery life of the overall profiler, updated central data storage, and extended profiling capabilities. The new module will address these requirements in the following ways:

1. Revamp the method of communication to improve data transfer volume and speed by offering a higher baud rate than the existing 9600 baud, and utilize the available 3G cell tower nearby.
2. Use a smaller integrated winch to release the sensor module to the water’s surface when broadcasting data, thus saving critical battery life by eliminating the need to surface the full profiler on a daily basis via the anchoring winch.
3. Relocate the full array of sensors to a smaller and less invasive module. This will allow the potential for profiling in both the up and down directions of movement. Currently, the profiler does not collect data while moving downward to prevent profiling water that has washed through the large 6 ft. by 2 ft. profiler assembly. This “washed-through” water is not representative of the environment around the profiler.
4. Provide a modern data storage unit and processor for aggregation of data, replacing the outdated and no longer produced Persistor module.

Success and stakeholder acceptance will be measured by benchmarking performance of the new module versus current-state performance. Notably, current-state data transfer is every 10th data point amounting to around 200kb of data with the majority of communication representing an “alive” signal that indicates whether the profiler is still functioning. Battery life is estimated between 3 weeks and 1 month, with the majority of power drain resulting from the anchoring winch. The project’s internal stakeholder is Dr. West, while the external stakeholder is Dr. Campbell and his team in Alaska.

Table 1. Stakeholder 2x2

Internal Stakeholders | External Stakeholders
Dr. West, Aquanauts | Dr. Campbell

Constraints are minimal. The intent of the long-term project with the research team is to design a new profiler as the existing profiler is no longer manufactured. The Aquanauts goal is to provide an ideal sensor and communication subsystem to address the research team’s requirements, rather than consider integration with other existing systems. Considerations will include data transfer rate, low power consumption, environmental survivability of the components in terms of temperature and pressure in a very cold underwater environment, and appropriate storage capacity to accommodate profiling data.

Table 2. QFD Chart

| Long-Range Communication | Centralized Data Storage and Processing | Extended Battery Life | Extended Profiling Capability | Total
Form Factor | 2 | 4 | 10 | 10 | 26
Power Consumption | 4 | 4 | 10 | 7 | 25
Environmental Conditions | 10 | 10 | 2 | 2 | 24
Total | 16 | 18 | 22 | 19

3. Technical Specifications

Table 3. Technical Specifications

Specification | Min | Max
Functional Temperature | -5 C | 30 C
Functional Depth | N/A | 100m
Total Power Consumption | 9 Vdc, 1.01 A (** Missing min amp info for RBR Brevio) | 14 Vdc, 1.67 A (**Missing max amp info for RBR Brevio)
Communication Range (Approx) | 100m (Operating depth + realistic estimate of surface buoy distance) | 8000m (Nearest cell tower, approximately 5 mi.)
Communication Frequency | GSM 850 MHz for remote 3G compatibility (869.2 – 893.8 MHz) Other available frequencies: E-GSM 1900 MHz, DCS 1800 MHz, PCS 1900 MHz

The specifications listed in Table 3 indicate the foundational requirements of the integrated system, including functional temperature, depth, power consumption, communication range, and communication frequency. All defined sections are equally important as they encompass environmental considerations for the underwater and highly remote locale, power consumption considerations in terms of saving critical battery life, and communications requirements for improved data transfer. The minimum power consumption is determined from the highest minimum operating voltage of all sensors, and maximum power consumption is determined from the lowest maximum operating voltage of all sensors. Minimum communication range is an approximation based on the operating depth of the profiler to a theoretical buoy containing additional communication equipment, and maximum communication range is from the profiler’s location to the nearest cell tower 5 miles (~8000 meters) away. The communication frequency, GSM 850 MHz, is the standard frequency used in data transfer to 3G cell towers.

4. Design Approach and Details
  4.1 Design Concept Ideation, Constraints, Alternatives, and Tradeoffs

The current design concept for this project is to have a central processor which will interface between the different sensors used by the profiler. The processor will store sensor data in a central place as well as interface with a cellular communication module to send the data out while profiling.

4.1.1 Smaller module

The current Prince William Sound profiler completely surfaces through the use of a winch. The winch is the greatest power draw and necessitates a large battery. One concept to conserve energy is to utilize a smaller module that surfaces to profile without surfacing with the battery. Through the use of a second winch, the large battery can remain at a lower depth, only needing to surface for charging. Since a smaller winch is used, less power will be expended. This smaller module will need to house the profiling sensors as well as a module for data transmission.

A constraint of a smaller module is the ability for it to withstand strong currents and storm conditions in the sound. The current profiler is sometimes overtaken by currents and is unable to surface and therefore cannot send a signal to indicate that it’s still working. When this occurs, the profiler needs to be checked on, which is a dangerous task especially under storm conditions. The sturdiness and surfacing abilities of the smaller module must be taken into account. If the separation of a smaller module from the profiler causes more issues when it comes to surfacing, the benefits of having a smaller module will be negated.

A few alternatives to the smaller module would be keeping the design as is and losing power saving capabilities, or having a buoy sitting at the surface to transmit messages. With the use of a buoy, the profiler would be able to stay submerged and use the buoy as a relay point for information. This would solve the problem of currents keeping the profiler from surfacing and allow for seamless communications with the shore. The buoy itself could have a solar powered battery so it doesn’t draw additional power from the profiler and therefore will not need to be serviced frequently. We decided against the use of a buoy because of the short lifespan previous buoys have had when utilized in the Prince William Sound. Previous buoys used by Dr. Campbell in the Prince William sound have only lasted around three weeks due to high boat traffic as well as strong weather conditions. Having to replace the buoy on a monthly basis would negate the benefits of using a buoy.

Table 4. Smaller Module Tradeoffs

Tradeoffs for Smaller module use
Pros | - Less power used - Safer than buoy use
Cons | - Added complexity - May not surface properly - no signal sent

4.1.2 Data Transmission

A data transmission module is a main focus for this project. Different concepts were considered, including satellite transmission for data, cellular telemetry and radio transmission. Cellular data is what is currently utilized for transmitting information from the profiler to shore. Using cellular data will make the most sense for application of this project. Since cellular data is currently utilized, it will be more ideal for use in testing as opposed to radio transmission and satellite transmission. There is a cellular tower near the sound that can support 3G communications.

While cellular data is useful to utilize, the constraint of inability to send data without surfacing still comes into play. Satellites would require a buoy and therefore a signal would persist even under harsher conditions. However, upon further inspection, satellites would be beyond the budget of this project and not many companies support satellite communication at such a remote location. Viasat, one of the larger and more affordable companies to offer satellite transmission, doesn’t immediately offer transmission to the sound [2]. Radio transmission is another option to explore, but would require testing and setup in the sound that would be hard to reproduce offsite.

Table 5. Cellular Data Tradeoffs

Tradeoffs for Cellular data usage
Pros | - In use currently - Easier to test
Cons | - Doesn’t work if the module doesn’t surface - May have lower speeds than other alternatives

4.1.3 Centralized Sensors

In order to successfully collect and store data as well as control the sensors and communications module, a central processor will be necessary. While there is one currently in use, it is no longer being produced. The plan for this project is to replace the old processor with one that is newer and can run a lightweight version of ubuntu in order to interface with some of the sensors.

One constraint to keep in mind are the conditions that this electronic component will be working under. The processor will be functioning at low temperatures and high pressure in an underwater environment. Special care needs to be taken to keep it in a waterproof enclosure and make sure any wiring or exposed pieces are protected.

An alternative would be to keep the current processor. Since it is no longer being produced and uses outdated software, it would be close to impossible to test the integration of sensors and communication modules. If any damage were to occur with the current processor, it would be harder to replace than something like an arduino or raspberry pi which are still in production.

Table 6. Updating Central Storage Tradeoffs

Tradeoffs for Updating central storage
Pros | - Old processor no longer in production - Can update software
Cons | - Added cost - Old processor still working and in use

  4.2 Preliminary Concept Selection and Justification

4.2.1 Smaller Module to Save Battery Life

After reviewing documentation and discussing the AMP needs with Dr. West and Dr. Campbell, the Aquanauts decided to design a module to ascend to the surface. One motivation for this was saving battery life. The profiler is rather large (diameter: 78.75 cm, length 212cm) [3] and uses much of the battery life to visit the surface. Since profiling occurs while travelling up the water column to the surface, this module must house the sensors needed for profiling. The module itself will need to be waterproof and sealed adequately to protect the electronics inside. The module will require a smaller winch to send the module to the surface and then back to the AMP. The module will also need to be connected to the power supply (currently the battery). This can be accomplished using a long cable with adequate protection/sleeving. The Aquanauts focus is moreso on the technology that will go inside this module and less on the mechanical aspects of this module.

4.2.2 Centralized Sensors

Currently, data from the sensors is stored in a central location using ASCII text. The main storage unit is a Persistor which is outdated and no longer produced. A new microcontroller must be chosen to accommodate the sensors on the module, cellular data transmission, expandable memory, and ease of programming. The sensors the microcontroller needs to interface with are: SBE 49 FastCAT CTD Sensor, RBR Brevio, Seabird Eco FLNTU, SBE 63 Optical Dissolved Oxygen Sensor, Aanderaa Oxygen Optode, and Seabird SUNA V2 Nitrate Sensor. The current plan is to use an Arduino Mega. This is best suited for this project because it has many pins to accommodate the sensors, expandable pin modules can be added if needed, there are multiple kits already developed for using cell data with Arduino, Arduino uses a C style language, and several Aquanauts have prior experience with Arduino. If an error occurs that makes the Arduino Mega no longer viable for the necessary functions, there are other models of Arduino and other microcontrollers such as Raspberry Pi that would be researched as replacements.

4.2.3 Data Transmission

When the module is at the surface, data from the sensors will be transmitted. Currently when the profiler surfaces, a nearby 3G cell tower is used to send minimal information. Due to availability and cost, the Aquanauts plan is to continue to use this cell tower for the increased data transmission. If this method ends up not being viable, there are backup methods such as satellite that can be further explored. The Aquanauts have selected the Arduino GSM 1400 Cellular Kit [4]. This kit is specifically designed to use the GSM/3G network which this module will be using. There are multiple attachments that can be used with an Arduino for cell data connection if there are issues with this kit.

  4.3 Engineering Analyses and Experiment

The Aquanauts team will perform simulations for both hardware and software for experiments on our design. The three Computer Engineers will be tasked with simulating the system in software, with programs and libraries that will operate on the final product. Once the three Electrical Engineers have designed the PCB, they will be in charge of performing tests on the hardware to make sure it will safely operate under certain power conditions. Power consumption can be monitored to determine how much power this module will be consuming. This is an important step as power should be saved using a smaller module.

In the next phase, the software and hardware teams will be able to test the overall system. In other words, we will perform experiments to make sure that the processing unit is able to send data through the new communication system. This will involve the use of real data that Dr. Campbell has collected. The Aquanauts will also ideally have access to real sensors which can be connected and used to simulate how the current profiling system works. This will prove that the current electronics will work with a new communication system and a centralized data processing unit.

  4.4 Codes and Standards

The relevant codes and standards include the following:

- IP69K: The IP (Ingress Protection) Code is an international standard that rates a product’s protection against intrusions by water and foreign particles. The 6 represents solid particle protection and the 9K represents the moisture protection. IP69K is rated as "dust tight" and protected against complete, continuous submersion in water [5].
  - The new modules that we introduce must be able to operate in continuous submersion.
- The Research Vessel Safety Standards (RVSS) appendix states that the tension in the rope must be monitored at the operator’s station with a resolution of a certain frequency depending on the factor of safety [6].
  - The rope of the winch must be able to meet the tension requirements with the addition of new modules.

802.15.4-2020 - IEEE Standard for Low-Rate Wireless Networks: The standard provides for ultra low complexity, ultra low cost, ultra low power consumption, and low data rate wireless connectivity among inexpensive devices, especially targeting the communications requirements of what is now commonly referred to as the Internet of Things [7].

5. Project Demonstration

To validate the specifications of the Prince William Sound Profiler Communication Module, a combination of software simulations, demonstration video, and a physical prototype with available components used to model the profiler will be used. Additionally, remote communication tests will be performed and software simulations will be used to validate the communication abilities of the communication module.

For the virtual senior design expo, the project demonstration will include the following: simulation results presented in a descriptive manner with important data highlighted to show that requirements have been met, a scaled down prototype of the profiler communication module to show how the system works, and video to provide demonstrations that can not be performed during the expo.

6. Schedule, Tasks, and Milestones:


Figure 1. PERT Chart showing the expected timeline for module development


Figure 2. Gantt chart for February 14th to March 20th showing a timeline of project phases and their estimated difficulty. Purple indicates low difficulty, yellow indicates medium difficulty, and red indicates high difficulty.


Figure 3. Gantt chart for March 21st to April 27th showing a timeline of project phases and their estimated difficulty. Purple indicates low difficulty, yellow indicates medium difficulty, and red indicates high difficulty.

The PWS profiler communication module will take advantage of pre-existing technology to upgrade a well documented profiler. Because our team is using established technology, our chance of success is not reliant on technological breakthroughs. The factor that has the largest chance of preventing success is falling behind schedule and hitting unexpected roadblocks. With the PERT chart and the Gantt chart establishing a timeline for the project, these roadblocks will be minimized. Considering the above factors, the team’s chance of finishing the project a week before the expo is 95%.

7. Marketing and Cost Analysis
  7.1 Marketing Analysis

The proposed communication module will be a newly designed long range wireless communication unit that will be an addition to a Sea Bird Thetis profiler currently deployed in the Prince William Sound. What is currently in use for external communications is an RS-232 100 Mbps serial to IP ethernet device. This sends a signal when the profiler itself surfaces.

There are some products that boast wireless communications without the necessity to leave the water. DSPComm has a line of underwater acoustic modems [8]. They are manufactured to be used underwater and can transmit a signal up to 3km away. Our product will not need to have such a long underwater range, as it can surface to transmit.

Another similar product on the market is the MarineLabs CoastScout. This long range communication buoy is a self-contained and self-powered buoy that is capable of transmitting 5MB wirelessly. The CoastScout is its own data collection device that collects weather and water data and sends it to a remote server. Our device differs from the CoastScout because instead of collecting its own data and sending it, it will be sending data that was collected by the underwater Thetis profiler. Additionally, the communication module will rely on power from the Thetis profiler battery instead of solar power.

  7.2 Cost Analysis

Currently, the group spends approximately three hours a week for meetings. These meetings are held to discuss the current status and the future goals of the project. Half of these meetings are held with our supervisor, Dr. West. This opportunity allows the group to receive feedback and produce an improved approach to the goal. Although the group works on reports and other documents during the meeting, some members may spend up to an additional hour adding to the report. Once the goals and the scope of the project have been solidified, each member will spend approximately eight hours a week to complete the tasks that were assigned. This time will still include the times spent for the meetings and the report documentation, but it will also be composed of times used to design the new components that the group aims to produce.

Table 7. Expected Costs

Part | Quantity | Manufacturer | Retailer | Price per Item | Total
Arduino Mega 2560 | 1 | Arduino | Arduino | $40.30 | $40.30
Arduino SIm MKR GSM 1400 Cellular Kit | 1 | Arduino | Newegg | $119.69 | $119.69
PRO Plus SD Card 32GB | 1 | Samsung | Amazon | $9.99 | $9.99
MKR SD Proto Shield | 1 | Arduino | Arduino | $13.80 | $13.80

8. Current Status

As of the time of submission of this proposal, it is estimated that the Aquanauts have completed about 20 percent of their project. Up to this point, the Aquanauts have a general design idea, but have not built anything yet. The design process will take place in the next phase.

The overall task of this project is to create a new communication system for the underwater profiler, which will be a major upgrade to the original system. Sub-tasks are listed below:

a. Designing a new centralized storage for all of the data in the profiler - IN PROGRESS
b. Designing a system that will send the data to the research facility over a cellular connection - IN PROGRESS
c. Designing software programs for the two components listed above - INCOMPLETE
d. Create a full BOM - IN PROGRESS
  i. Order parts - INCOMPLETE
e. Project proposal and presentation - IN PROGRESS
9. Leadership Roles
a. Group Leader: Jim O’Donnell
- Main speaker and scheduling coordinator
b. Expo Coordinator: Shayna Seidel
- In charge of making sure the team is aware of all requirements for the expo
c. Financial Advisor: Seungju Jason Lee
- Responsible for keeping track of receipts and handling reimbursements
d. Webmaster: Ruben Quiros
- Responsible for managing the team’s website
e. Documentation Coordinator: Timothy Pierce
- In charge of maintaining and submitting documentation on behalf of the group
f. Tech lead: Shelby Crisp
- Host and manager of the git repository
10. References
1. R. W. Campbell, P. L. Roberts, and J. Jaffe, “Prince William Sound Plankton Camera: a profiling in situ observatory of plankton and particulates,” OUP Academic, 24-Mar-2020. [Online]. Available: https://academic.oup.com/icesjms/article/77/4/1440/5811106. [Accessed: 17-Feb-2021].
2. Admin, “How it Works: The technology behind satellite internet,” Viasat.com. [Online]. Available: https://www.viasat.com/about/newsroom/blog/how-it-works-the-technology-behind-satellite-internet/. [Accessed: 18-Feb-2021].
3. S.-B. S. USA, “Thetis Autonomous Moored Profiler Datasheet,” Sea-Bird Scientific. [Online]. Available: https://www.seabird.com/systems/thetis-profiler/family-downloads?productCategoryId=54627869948. [Accessed: 17-Feb-2021].
4. ARDUINO SIM - MKR GSM 1400 Cellular Kit. [Online]. Available: https://store.arduino.cc/usa/sim-bundle. [Accessed: 17-Feb-2021].
5. H. H. A. K. A. www.crazyhamster.co.uk, IP Ratings Explained - know your enclosure Ingress Protection ratings. [Online]. Available: https://www.enclosurecompany.com/ip-ratings-explained.php. [Accessed: 17-Feb-2021].`
6. “Winch and wire regulations,” Scripps Institution of Oceanography. [Online]. Available: https://scripps.ucsd.edu/ships/planning/winch-and-wire. [Accessed: 17-Feb-2021].
7. “802.15.4-2020 - IEEE Standard for Low-Rate Wireless Networks,” IEEE Xplore. [Online]. Available: https://ieeexplore.ieee.org/document/9144691/metrics#metrics. [Accessed: 18-Feb-2021].
8. “Products,” Underwater Wireless Modem and Communication Devices, 05-Feb-2021. [Online]. Available: http://www.dspcommgen2.com/products/. [Accessed: 18-Feb-2021].
9. Xylem, Aanderaa Oxygen Optode 4531. Xylem, Bergen, Norway, 2020. Datasheet. https://www.aanderaa.com/productsdetail.php?Oxygen-Optodes-2
10. Xylem, Aanderaa Oxygen Optode 4835. Xylem, Bergen, Norway, 2020. Datasheet. https://www.aanderaa.com/productsdetail.php?Oxygen-Optodes-2
11. RBR, RBRBrevio C.T.D. RBR, Ottawa, Ontario, 2019. Datasheet. https://rbr-global.com/products/standard-loggers/rbrbrevio
12. Seabird, ECO FLbb Fluorometer and Scattering Meter. Seabird, Bellevue, WA, 2021. Datasheet. https://www.seabird.com/combination-sensors/eco-flntu/family?productCategoryId=54758054352
13. Seabird, SBE 49 FastCAT CTD Sensor. Seabird, Bellevue, WA, 2015. Datasheet. https://www.seabird.com/profiling/sbe-49-fastcat-ctd-sensor/family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
14. Seabird, SBE 63 Optical Dissolved Oxygen Sensor. Seabird, Bellevue, WA, 2014. Datasheet. https://www.seabird.com/oxygen-sensors/sbe-63-optical-dissolved-oxygen-sensor/family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
15. Seabird, SUNA V2 UV Nitrate Sensor. Seabird, Bellevue, WA, 2017. Datasheet. https://www.seabird.com/nutrient-sensors/suna-v2-nitrate-sensor/family?productCategoryId=54627869922

Appendix

Sensor | Min Voltage | Max Voltage | Min Amps | Max Amps | Min Temp | Max Temp | Max Depth | Notes
Aandera Optode 4531 (RS-232) | 5 Vdc | 30 Vdc | 0.16 mA + 40 mA/S | 100mA | -5 C | 30 C | 100m | RS-232 output format
Aandera Optode 4531 (Analog) | 7 Vdc | 30 Vdc | 0.16 mA + 40 mA/S | 100mA | -5 C | 30 C | 100m | Analog output format
Aandera Optode 4835 | 5 Vdc | 14 Vdc | 0.16 mA + 48 mA/S | 100mA | -5 C | 40 C | 300m | RS-232 output format
RBR Brevio | 4.5 V | 30 V | ??? | ??? | -5 C | 35 C | 750m (Plastic), 6000m (Titanium) | RS-232 output format
Searbird ECO FLbb Fluorometer | 7 Vdc | 15 Vdc | 140 µA | 60 mA | ??? | ??? | 600m | RS-232 output format, 19200 baud
Seabird SBE 49 FastCAT CTD Sensor | 9 Vdc | 24 Vdc | 350 mA (9V), 285 mA (12V), 180 mA (19V) | 750 mA (Turn-on transient) | -5 C | 35 C | 350m (Plastic), 7000m (Titanium) | RS-232 output format
Seabird SBE 63 Dissolved Oxygen Sensor | 6 Vdc | 24 Vdc | 35 mA | 35 mA | 0 C | 30 C | 600m (Plastic), 7000m (Titanium) | RS-232 output format
Seabird SUNA V2 UV Nitrate Sensor | 8 Vdc | 18 Vdc | 625 mA (12V) | 625 mA (12V) | 0 C | 35 C | 500m | Serial data output, assuming RS-232
**mA/S is milliamps per sampling interval in seconds | | | Total min amps (mA) | Total max amps (mA) | Overall Min Temp | Overall Max Temp | Overall Max Depth
| | | 1010.62 | 1670 | 0 C | 30 C | 100m

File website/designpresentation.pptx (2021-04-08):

## Prince William Sound Profiler Mid-semester Design Review

ECE 4873 Senior Design Project
Aquanauts

## Introduction

- 1989 Exxon Valdez oil spill caused environmental damage
- Since 2013 an autonomous moored profiler (AMP) has collected data on PWS recovery
- Profiler needs modifications/updates
- Goals:
- Updated data storage and transmission capabilities for existing profiler
  - Module can send data from profiler sensors to scientists
  - Centralized data storage in module
- Relay system to supply power to sensors on-demand

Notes: Shayna

## Project Description and Goals

- Customer Requirements
  - Higher data transfer volume and speed
  - Updated central memory and processing
  - Automated system to turn sensors on/off on a schedule
- How we will address each
  - Revamp communications utilizing the nearby 3G/4G cell tower and updated data transfer rates vs. current 2G utilization
  - Direct FTP of data will provide full data transfer vs. the current direct UDP packetized transfer only representing 1/10th of collected data
  - Updated memory and processing unit to replace outdated/no longer manufactured Persistor
    - Raspberry Pi 3B
    - Samsung 870 EVO Solid State Drive
  - Custom-built MOSFET switching board to supply power to on-board sensors on a schedule
    - Conserves battery life

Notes: jim

## Technical Specification

Table 3. Technical Specifications

Specification | Min | Max
Functional Temperature | -5 C | 30 C
Functional Depth | Sea level | 60m
Total Power Consumption | 9 Vdc, 1.01 A | 14 Vdc, 1.67 A
Communication Range (Approx) | 8000m (Nearest cell tower, approx. 5 miles) | N/A
Communication Protocol | 3G & 4G SFTP (Direct to local server, or to cloud)

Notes: Jim

## Design Approach and Details

- Update Processor
  - Raspberry Pi 3B
    - Choice considerations:
      - Lowest power consumption of RPi models that support Linux
      - Linux required for ftp & ssh protocols
      - Arduino does not support Linux
      - USB bootable from SSD
    - Cons
      - Power consumption still not optimal (~210mA at idle)

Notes: Jim

## Design Approach and Details Cont’d

- Data Transmission
  - Raspberry Pi communicating with 3G/4G cell tower via SixFab Cellular Communications Module and antennas
  - SFTP to Cloud storage, or transmit direct to local server in Alaska
    - Cloud storage may require paid subscription, but not dependent on state of local server in Alaska, also will act as data backup
    - Local server in Alaska requires user setup/maintenance, data transmission success relies on state of local server
  - Cons:
    - Hard to test whether or not the signal in Alaska is strong enough

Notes: Shelby

## Design Approach and Details - SSD

- SSD is preferred over SD card for the following reasons:
  - Longevity -- SDs with DRAM cache last significantly longer than SD cards
    - They also have longer warranties
  - Size -- The system will have more storage to collect more data
    - Size also increases longevity
  - Performance -- SSDs have faster read and write speeds
    - This will help to run programs more efficiently
- Samsung 870 EVO (256 GB)
  - Has DRAM cache, good size, noted performance in user reviews, and 5 year warranty

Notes: Ruben

## Communications Diagram

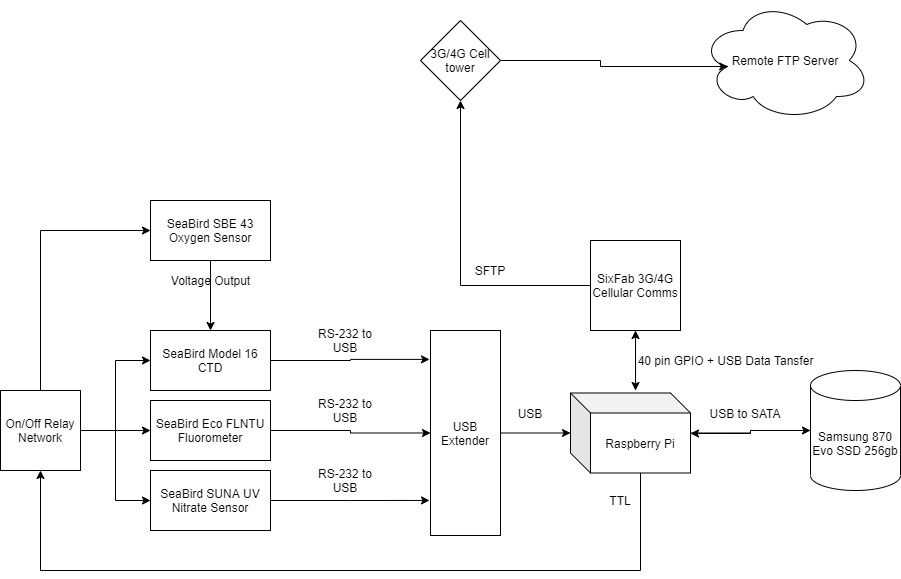
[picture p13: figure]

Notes: Shelby

## Design Approach and Details - MOSFET Board

- Buck converter to step down the voltage from the battery from 30V to 12V
  - Isolation capable buck converter with adjustable voltage
  - All sensors on the profiler can operate on 12V
- Individual MOSFETS will be used to turn individual sensors on and off
  - MOSFETs instead of relays
    - Since the battery voltage will be stepped down using an isolated buck converter, additional electric isolation is not required
    - The power MOSFETs can be simulated, but it was difficult to find spice models for SSRs
- MOSFET board will allow for new sensors to be added to the profiler in the future

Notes: Tim

## MOSFET Switching Simulation

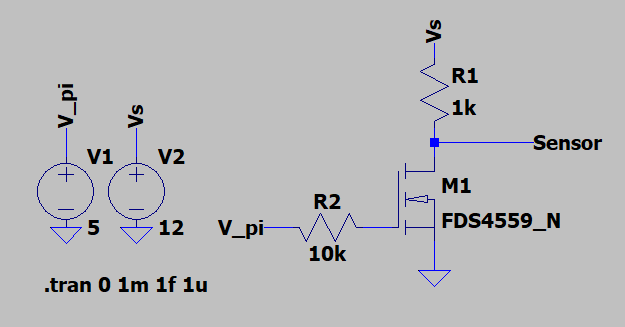
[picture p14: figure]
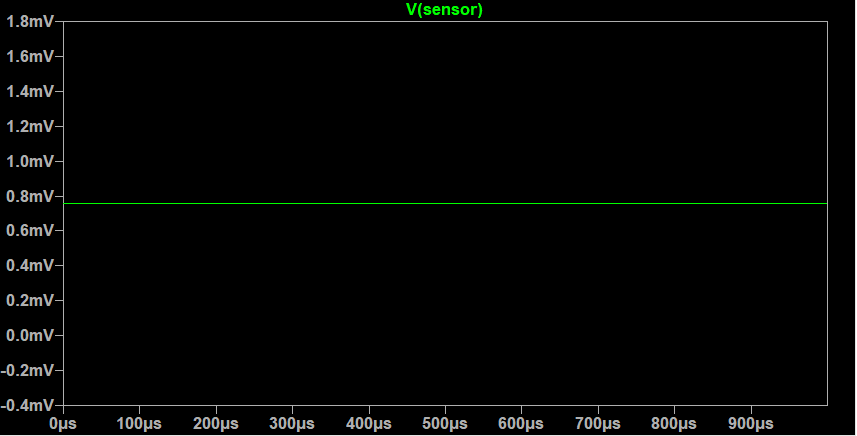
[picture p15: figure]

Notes: Jason

## MOSFET Switching Simulation (Continued)

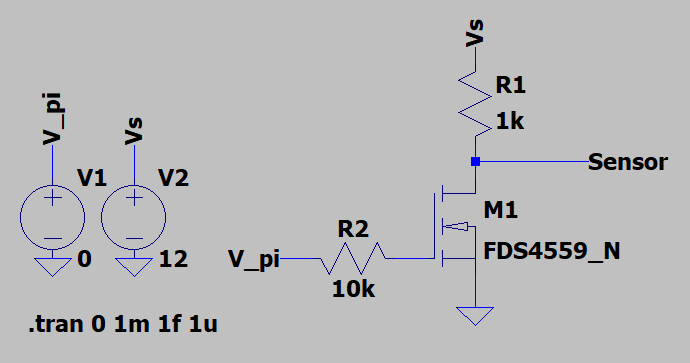
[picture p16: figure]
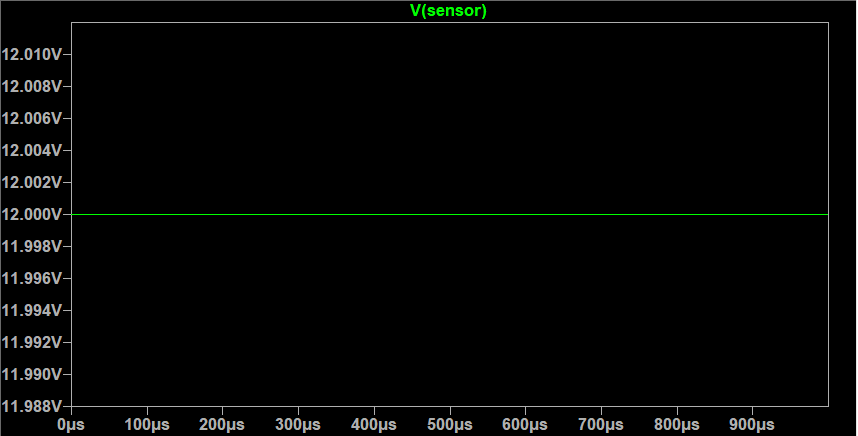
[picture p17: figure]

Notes: JAson

## Power Diagram

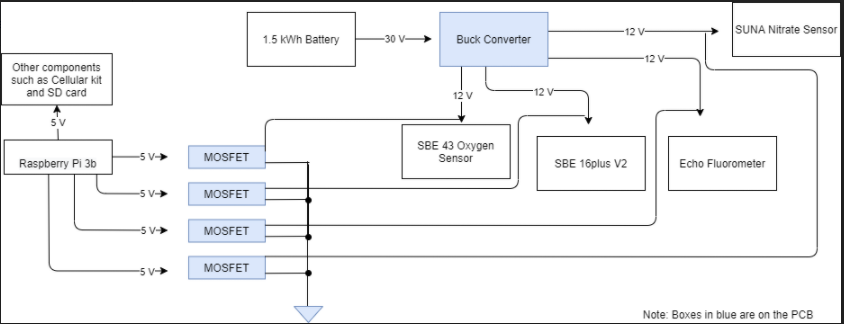
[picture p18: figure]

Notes: Shayna

## Codes and Standards

- 802.15.4-2020 - IEEE Standard for Low-Rate Wireless Networks: The standard provides for ultra low complexity, ultra low cost, ultra low power consumption, and low data rate wireless connectivity among inexpensive devices.
- IMT-2000: Offers the capability of providing value-added services and applications for frequencies between 400 MHz and 3 GHz.
  - Makes 3G systems affordable
  - Adds compatibility feature with existing systems such as 2G

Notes: Jason

## Project Demonstration

- Verification and Validation
  - Software simulation and physical testing with the final prototype (Inspect, Demonstrate, Test)
- Expo
  - Poster, Video, Prototype Demo
    - Present simulation results in a descriptive manner
    - Video demo for features not easily demonstrated during the Expo
    - Physical prototype

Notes: Shayna

## Schedule, Tasks, and Milestones

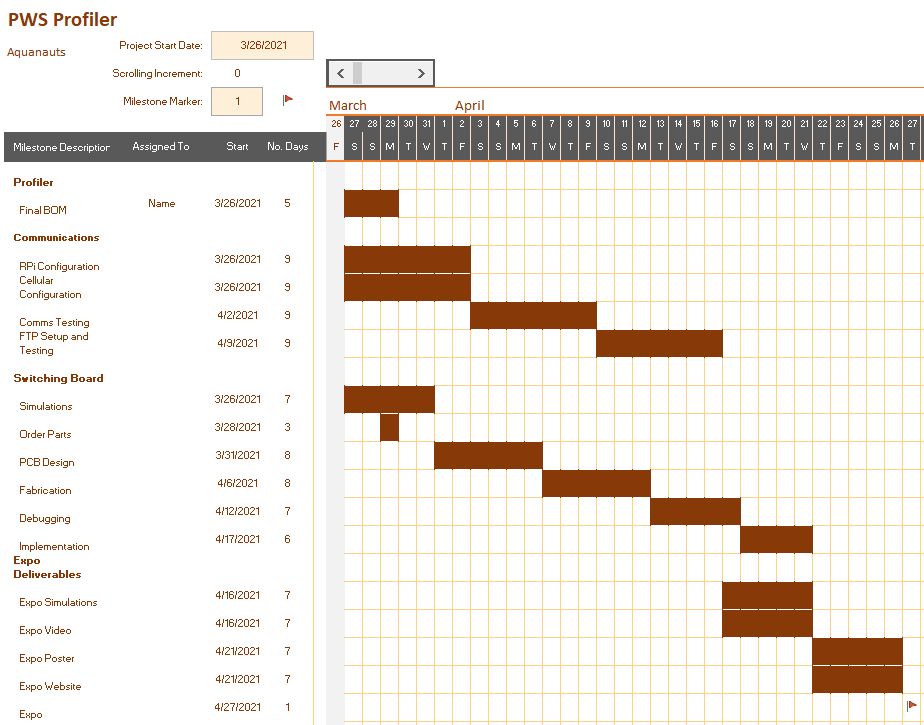
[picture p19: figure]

Chance of Success: 95%

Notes: Tim

## BOM

Part | Manufacturer | Retailer | Price per Item | Quantity | Part Total
Raspberry Pi 3B | Raspberry Pi | Digi-Key | 35 | 1 | 35
Raspberry Pi 4G/LTE Cellular Modem Kit | Sixfab | Sixfab | 109 | 1 | 109
Sixfab Connect Sim | Sixfab | Sixfab | 2 | 1 | 2
SAMSUNG PRO Plus SDHC Full Size SD Card 32GB | Samsung | Amazon | 9.99 | 1 | 9.99
MKR SD PROTO SHIELD | Arduino | Arduino | 13.8 | 1 | 13.8
USB 3.0 SATA III Hard Drive Adapter Cable, SATA to USB Adapter Cable | SKL Tech | Amazon | 7.99 | 1 | 7.99
SAMSUNG 870 EVO 250GB 2.5 Inch SATA III Internal SSD | Samsung | Amazon | 39.99 | 1 | 39.99
DC-DC Converter | Mean Well USA | Digi-Key | 26.71 | 1 | 26.71
Power MOSFET FQP30N06L | ON Semiconductor | Digi-Key | 1.22 | 4 | 4.88
USB to Serial RS232 Adapter | SIIG | Amazon | 49.85 | 1 | 49.85

Total
299.21

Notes: Jason

## Current Status

a. Full analysis of power requirements - COMPLETE
b. PCB design - IN PROGRESS
c. Communication Design - COMPLETE
  i. Testing phase - IN PROGRESS
d. Software & processing - IN PROGRESS
e. Creating a full BOM - NEARLY COMPLETE
  i. Order parts - NEARLY COMPLETE (Need RS-232 hub & buck converters)

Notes: Ruben

## Leadership Roles

- Group Leader: Jim O’Donnell
- Expo Coordinator: Shayna Seidel
- Financial Advisor: Seungju Jason Lee
- Webmaster: Ruben Quiros
- Documentation Coordinator: Timothy Pierce
- Tech lead: Shelby Crisp

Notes: Ruben

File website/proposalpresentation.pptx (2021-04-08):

## Prince William Sound Profiler Communication Module

ECE 4873 Senior Design Project
Aquanuats

## Introduction

- 1989 Exxon Valdez oil spill caused environmental damage
- Since 2013 an autonomous moored profiler (AMP) has collected data on PWS recovery
- Profiler needs modifications/updates
- Goal: design new communication module for existing profiler
- Module can send data from profiler sensors to scientists
- Centralized data storage in module
- Requesting $400, preliminary cost estimate is $183.78
  - PCB printing cost, other components, and shipping will increase cost

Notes: Shayna

## Project Description and Goals

- 2 main customer requirements, 2 auxiliary requirements:
  - Higher data transfer volume and speed (M)
  - Longer battery life (M)
  - Updated central memory and processing (A)
  - Improved profiling ability (A)
- How we will address each:
  - Revamp comms utilizing the nearby 3G cell tower and updated data transfer rates. Current - 9600 baud, proposed 56,000 to 114,000 baud (Arduino GSM shield specs)
  - One main sensor module operating on separate winch. This will accomplish two things:
    - Better battery life - reduce use of larger anchoring winch by only surfacing the sensor module for comms
    - Ability to profile on the way down by preventing water wash through profiler
  - Updated memory and processing unit to replace outdated/no longer manufactured Persistor

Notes: jim

## Technical Specification

Table 3. Technical Specifications

Specification | Min | Max
Functional Temperature | -5 C (** Datasheet says 0) | 30 C
Functional Depth | N/A | 100m
Total Power Consumption | 9 Vdc, 1.01 A (** Missing min amp info for RBR Brevio) | 14 Vdc, 1.67 A (**Missing max amp info for RBR Brevio)
Communication Range (Approx) | 100m (Operating depth + realistic estimate of surface buoy distance) | 8000m (Nearest cell tower, approximately 5 mi.)
Communication Frequency | GSM 850 MHz for remote 3G compatibility (869.2 – 893.8 MHz) Other available frequencies: E-GSM 1900 MHz, DCS 1800 MHz, PCS 1900 MHz

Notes: Questions:

Need power req’s for RBR Brevio
Which optode sensor is being used, or both? Link had 4531 and 4835

## Design Approach and Details

- Smaller Module
  - Design
    - Connected to power supply via a long cable
    - Aquanauts focus is on technology inside module and not the enclosure
  - Pros
    - Will save battery life
    - Safer than using a buoy
  - Cons
    - May not surface properly to send signals
- Centralized sensors
  - Design
    - Currently using outdated persistor
    - New microcontroller- Arduino Mega
  - Pros
    - Update older sensor
      - Allow for replacement
  - Cons
    - Added Cost

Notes: Shayna + shelby

## Design Approach and Details Cont’d

- Data Transmission
  - Design
    - Considered Satellite and Radio
    - Nearby 3G cell tower
    - Arduino GSM 1400 Cellular Kit
  - Pros
    - Currently in use
    - Easier to test
  - Cons
    - Doesn’t work if module doesn’t surface

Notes: Shayna + shelby

## Codes and Standards

- IP69K: Ingress Protection rating that states that the device will be dust-tight and will be protected against complete, continuous submersion.
- The Research Vessel Safety Standards (RVSS) states that the tension in the rope must be monitored at the operator’s station with a resolution of a certain frequency depending on the factor of safety.
- 802.15.4-2020 - IEEE Standard for Low-Rate Wireless Networks: The standard provides for ultra low complexity, ultra low cost, ultra low power consumption, and low data rate wireless connectivity among inexpensive devices.

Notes: Jason

## Project Demonstration

- Verification and Validation
  - Software simulation and physical testing with the final prototype (Inspect, Demonstrate, Test)
- Expo
  - Poster, Video, Prototype Demo
    - Present simulation results in a descriptive manner
    - Video demo for features not easily demonstrated during the Expo
    - Physical prototype

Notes: Tim

## Schedule, Tasks, and Milestones Pt. 1


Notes: Tim

## Schedule, Tasks, and Milestones Pt. 2


Chance of Success: 95%

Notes: Tim

## Marketing and Cost Analysis

Some similar products on market
- DSPComm underwater acoustic modem
  - Used underwater
  - Transmit signal 3 km away
- MarineLabs CoastScout
  - Long range communication buoy
  - 5 MB wirelessly
  - Use of buoy isn’t optimal due to boat traffic and weather conditions

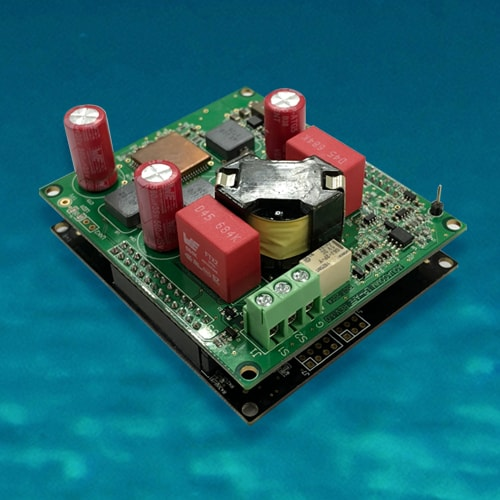
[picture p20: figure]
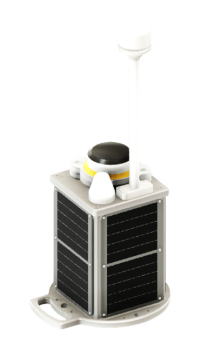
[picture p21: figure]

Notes: Shelby pt 1 Tim pt 2

## Preliminary BOM

Part | Quantity | Manufacturer | Retailer | Price per Item | Total
Arduino Mega 2560 | 1 | Arduino | Arduino | $40.30 | $40.30
Arduino SIm MKR GSM 1400 Cellular Kit | 1 | Arduino | Newegg | $119.69 | $119.69
PRO Plus SD Card 32GB | 1 | Samsung | Amazon | $9.99 | $9.99
MKR SD Proto Shield | 1 | Arduino | Arduino | $13.80 | $13.80

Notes: Jason

## Current Status

a. Designing a new centralized storage component for data - IN PROGRESS
b. Designing a system that will send data to the research facility over a cellular connection - IN PROGRESS
c. Designing software programs for components listed above - INCOMPLETE
d. Creating a full BOM - IN PROGRESS
  i. Order parts - INCOMPLETE

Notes: Ruben

## Leadership Roles

- Group Leader: Jim O’Donnell
- Expo Coordinator: Shayna Seidel
- Financial Advisor: Seungju Jason Lee
- Webmaster: Ruben Quiros
- Documentation Coordinator: Timothy Pierce
- Tech lead: Shelby Crisp

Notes: Ruben

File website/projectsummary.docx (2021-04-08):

ECE4873 Project Summary

Project Title | Prince William Sound Profiler
Team Members (names and majors) | Seungju Jason Lee, EE
| James O’Donnell, CompE
| Ruben Quiros, CompE
| Shelby Crisp, CompE
| Shayna Seidel, EE
| Timothy Pierce, EE
Course & Section Primary Advisor | ECE4873A Dr. Mick West
Semester | Spring 2021
Web Site URL | PENDING

Project Abstract

(250-300 words)

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

Project Title | Prince William Sound Profiler
List codes and standards that significantly affect your project. Briefly describe how they influenced your design. | If we pursue working on a communication component, we will need to adhere to IEEE 802.11: for wireless communications from profiler to shore. Since we are creating a submersible electric component, we will need to adhere to electronic waterproofing standards
List at least two significant realistic design constraints that applied to your project. Briefly describe how they affected your design. | Two constraints are water and pressure. Everything we design that must go underwater needs to be able to withstand water and the corresponding pressure at the given depth. This is especially important for electronic components. Other constraints are water temperature and water current. All components on the profiler will need to be able to operate in low temperatures. All parts of the profiler will also need to be able to reach the surface despite the strength of the current.

Briefly explain two significant trade-offs considered in your design, including options considered and the solution chosen.

One tradeoff we have to consider is that adding any additional module will increase the power consumed. Since the battery at this point must be changed frequently, we have to consider efficiency of added components. One solution to the issue could be that we develop an improved power system that will allow the profiler to operate for a longer period of time compared to the current iteration despite having additional modules.

Another tradeoff is that the longer our profiler or any component stays at the surface, the higher the risk of damage is. This is caused by high boat traffic in the area. A possible solution is optimization of any task that needs to be performed at surface as well as limiting any component that needs to stay at surface level.

Briefly describe the computing aspects of your projects, specifically identifying hardware-software tradeoffs, interfaces, and/or interactions.

Complete if applicable; required if team includes CmpE majors.

While the current system already uses machine learning to gather data on plankton ecosystems, our task is to improve upon what is already in place. The originally created neural network algorithm has not been updated since 2019, so there is a possibility that there are new libraries available to upgrade the current system. If we are given the original source code, we will be able to look for any sections of the program(s) that can be optimized, as well.

The current profiler also makes use of a fairly primitive communication system, only sending a short signal to indicate that it’s still in operation once every 24 hours. We would like to implement a new communication system that can better send stronger signals without a large drain on power. We will need to create a module that can collect pertinent information from both the camera and water tester, create one or more data packets, and transmit these messages either to a relay point on shore or find a way to create reliable communication otherwise.

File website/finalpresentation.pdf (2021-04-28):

# Prince William Sound Underwater Profiling Vehicle

## The Aquanauts

Jason Lee, Jim O’Donnell, Ruben Quiros, Shayna Seidel, Shelby Crisp, and Timothy Pierce

# Background: Prince William Sound

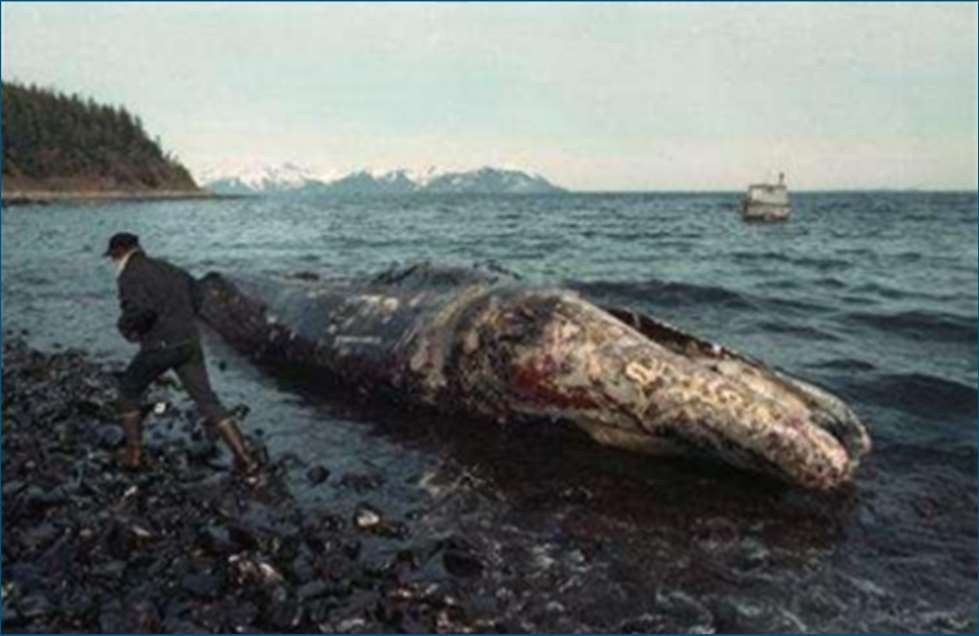
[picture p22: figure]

- In 1989 the Exxon Valdez oil tanker
crashed into Bligh Reef, spilling

### 10.8 million gallons of oil in PWS

- Many species and industries were affected by this disaster
- There has been improvement over the years, but PWS is still in recovery

# Background: Profiler

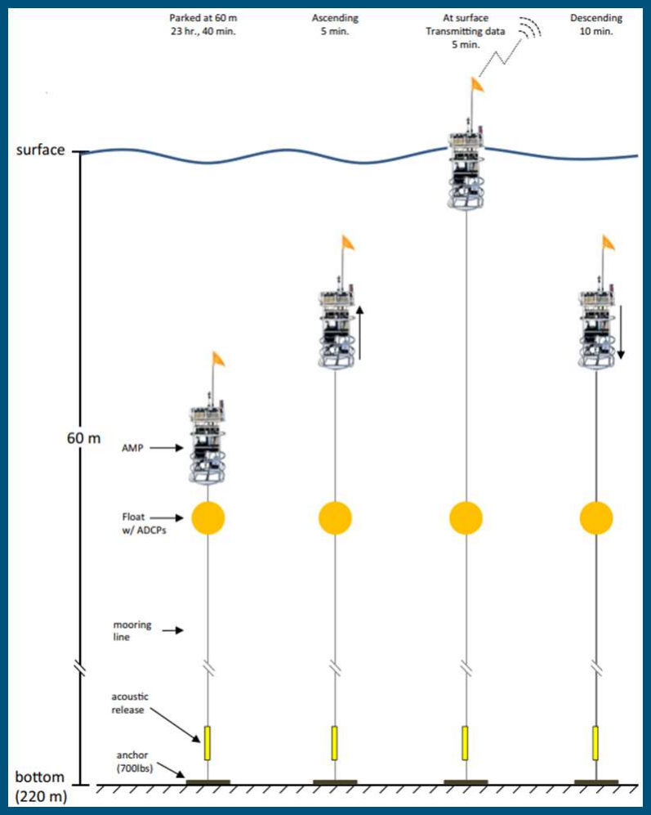
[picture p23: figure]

- Since 2013 Ocean scientists have used an autonomous moored
profiler (AMP) to collect
environmental data on the
recovery of PWS
- The profiler has an anchor that holds it at a specified depth
- The profiler ascends to the surface once a day to collect data and transmit a signal that it is still alive

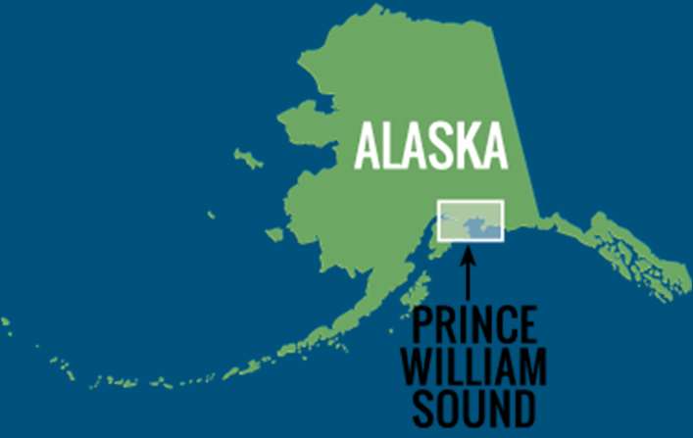
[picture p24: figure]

# Problems

- Only 1/10th of data is currently being transferred remotely
- Someone must travel to the platform every few weeks in order to extract data
- This trip can be difficult and dangerous
- The data processing components are outdated
- The profiler does not have the flexibility to turn on/off individual sensors (save battery life)

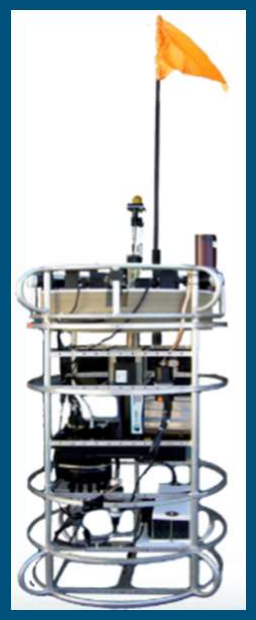
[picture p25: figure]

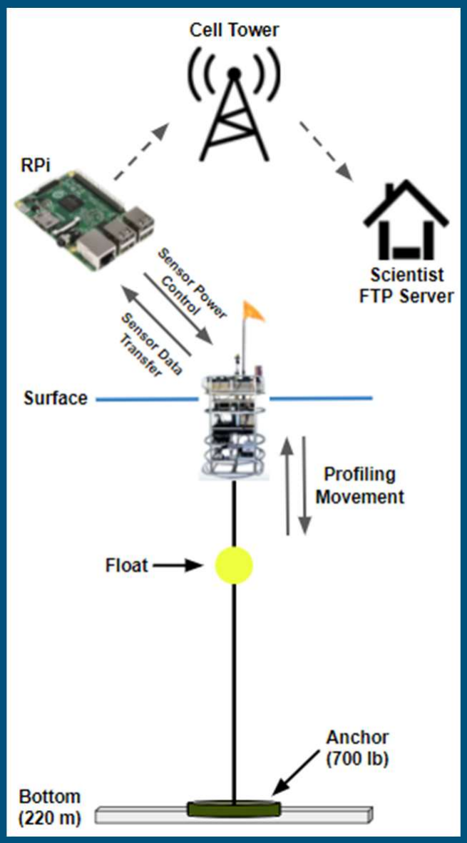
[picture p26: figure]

# Our Solution

- Update the microcontroller to accommodate modern cellular capabilities and data storage
- Raspberry Pi 3B running Raspbian (Lightweight Debian Linux)
- Transmit 100% of data to ocean scientists via FTP over a cellular connection
- Not considering plankton camera
- Custom PCB to power microcontroller & enable sensors on a schedule from the profiler’s on-board battery
- Signal to enable or disable sensor from Raspberry Pi



# PCB


# Raspberry Pi and PCB


# Results (Simulation)


# Results (Experimental)


Part | Manufacturer | Retailer | Price per Item | Quantity | Part Total
Raspberry Pi 3B | Raspberry Pi | Amazon | 37.99 | 1 | 37.99
Raspberry Pi 4G/LTE Cellular Modem Kit | Sixfab | Sixfab | 109 | 1 | 109
Sixfab Connect Sim | Sixfab | Sixfab | 2 | 1 | 2
SAMSUNG PRO Plus SDHC Full Size SD Card 32GB | Samsung | Amazon | 9.99 | 1 | 9.99
MKR SD PROTO SHIELD | Arduino | Arduino | 13.8 | 1 | 13.8
USB 3.0 SATA III Hard Drive Adapter Cable, SATA to USB Adapter Cable | SKL Tech | Amazon | 7.99 | 1 | 7.99
SAMSUNG 870 EVO 250GB 2.5 Inch SATA III Internal SSD | Samsung | Amazon | 39.99 | 1 | 39.99
30 W DC/DC Converter | Mean Well USA | Digi-Key | 26.71 | 1 | 26.71
FQP30N06L | ON Semiconductor | Digi-Key | 1.22 | 6 | 7.32
USB to Serial RS232 Adapter | SIIG | Amazon | 49.85 | 1 | 49.85
12 W DC/DC Converter | Traco Power | Digi-Key | 28 | 1 | 28
PCB | JLC PCB | JLC PCB | 14.8 | 1 | 14.8
500 mA Fuse | Bel Fuse Inc | Digi-Key | 0.234 | 5 | 1.17
1A Fuse | Bel Fuse Inc | Digi-Key | 0.224 | 5 | 1.12
5x20 mm Fuse Holder | Würth Elektronik | Digi-Key | 0.64 | 8 | 5.12

Total

354.85


## Special thanks to Dr. West and Dr. Campbell


# Questions?




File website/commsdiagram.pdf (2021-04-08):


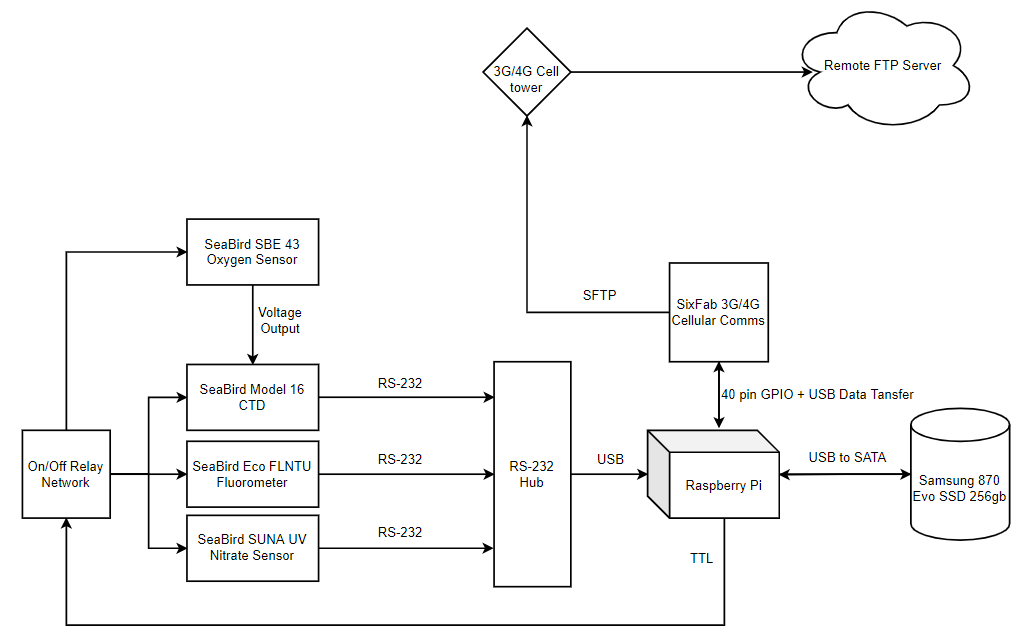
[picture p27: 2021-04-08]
website/commsdiagram.PNG

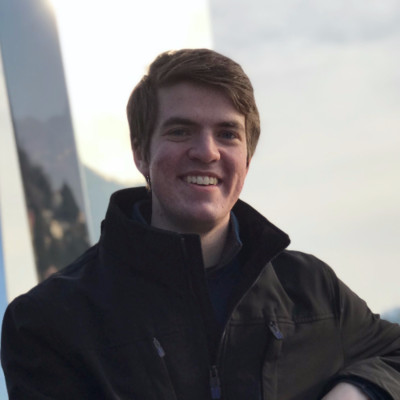
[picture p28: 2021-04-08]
website/tim-headshot.jpg

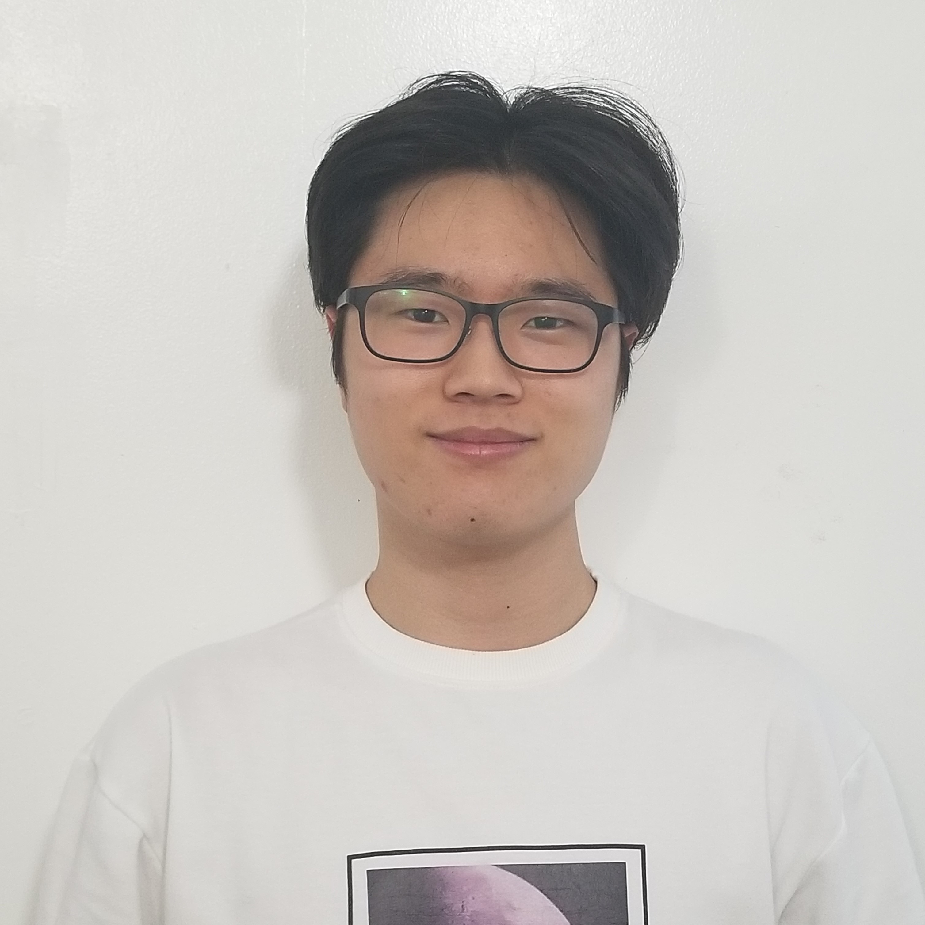
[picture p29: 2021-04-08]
website/jason-headshot.jpg

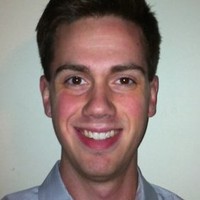
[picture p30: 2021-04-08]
website/jim-headshot.jpg

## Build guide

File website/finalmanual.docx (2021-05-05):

Manual for PWS Communications Module

ECE 4873 Senior Design

Aquanauts

Dr. Mick West

Dr. Robert Campbell

Shayna Seidel, EE, sseidel7, sseidel7@gatech.edu

Jim O’Donnell, CmpE, jodonnell3, jodonnell3@gatech.edu

Shelby Crisp, CmpE, scrisp3, scrisp3@gatech.edu

Jason Lee, EE, slee3117, slee3117@gatech.edu

Ruben Quiros, CmpE, rquiros6, rquiros6@gatech.edu

Timothy Pierce, EE, tpierce31, timrpierce31@gatech.edu

Table of Contents

1. Introduction and Intended Use ………………………………………………….. 4
2. Setup ………………………………………………………………………………. 5

2.1 Raspberry Pi, Cellular Kit, and SSD Instructions …………………………….. 5

2.2 PCB Instructions ……………………………………………………………... 7

3. How to Use ………………………………………………………………………... 9

3.1 Telit Commands ……………………………………………………………… 9

3.2 Quectel Commands …………………………………………………………... 11

3.3 Benefits to Using the Quectel Chip …………………………………………... 13

3.4 Turning sensors on and off …………………………………………………… 13

4. Monitoring the Sixfab Cell Kit ……………………………………………..…… 16
5. References ………………………………………………………………………… 17

Appendix …………………………………………………………………………… 18

Nomenclature

CmpE: Computer Engineer

EE: Electrical Engineer

PCB: Printed Circuit Board

Pi: Raspberry Pi 3B

PWS: Prince William Sound

SSD: Solid State Drive

Manual for Communication Module

1. Introduction and Intended Use

This communication module is intended to be used for the Profiler located in Prince William Sound, which is monitored by Dr. Robert Campbell. This new module will replace the old Persistor processor and relay system with a Raspberry Pi 3B, Sixfab cell kit, and a MOSFET switching system on a PCB. The updated system will give the system more processing power for increased data collection, a stronger stable cellular connection to send more data using 3G/4G, and a subsystem that allows the research team to turn sensors on and off individually. Technological capabilities were increased, but with power consumption that is nearly similar to the original Persistor module.

2. Setup

The following parts are needed to run this prototyped system:

1) Raspberry Pi 3B with its external power supply (rated at 2.5 Amps and 5.25 V)
2) Minimum 16GB Micro SD Card
3) Samsung 870 EVO 250 GB SSD
4) SATA to USB cable
5) Sixfab cell kit with its external power supply (rated at 2.5 Amps and 5.25 V)
6) Printed Circuit Board (for details, see the Aquanauts’ final report)
7) Micro USB to Micro USB cable

2.1 Raspberry Pi, Cellular Kit, and SSD Instructions

1. Flash both an SD Card and the SSD with your chosen version of Linux. More information can be found at the following link: Installing operating system images - Raspberry Pi Documentation (https://www.raspberrypi.org/documentation/installation/installing-images/) Note: The SD Card is only required for initial setup, and is not required for permanent use of the Raspberry Pi.
2. For the Raspberry Pi 3B, a bit in the One Time Programmable memory must be set in order to enable booting from USB (booting from the SSD). This will require initially booting the Raspberry Pi 3B from an SD Card. More information can be found at the following link in the “Raspberry Pi 2B v1.2, 3A+, 3B, Computer Module 3, 3+” section: USB mass storage boot - Raspberry Pi Documentation (https://www.raspberrypi.org/documentation/hardware/raspberrypi/bootmodes/msd.md)
  a. For our chosen SSD, boot time took slightly longer than the default boot time of 2 seconds. This causes boot issues occasionally for the following reason:

USB enumeration is a means of enabling power to the downstream devices on a hub, then waiting for the device to pull the D+ and D- lines to indicate if it is either USB 1 or USB 2. This can take time: on some devices it can take up to three seconds for a hard disk drive to spin up and start the enumeration process. Because this is the only way of detecting that the hardware is attached, we have to wait for a minimum amount of time (two seconds).

  b. This issue can be resolved using the following. Note: this change must initially be made on the SD Card when configuring boot options, and is also recommended to be made on the SSD itself. More information regarding boot sequence and timing can be found at the following link: Boot sequence - Raspberry Pi Documentation (https://www.raspberrypi.org/documentation/hardware/raspberrypi/bootmodes/bootflow.md)

If the device fails to respond after this maximum timeout, it is possible to increase the timeout to five seconds using program_usb_boot_timeout=1 in config.txt.

3. Establish connection between all parts:
  a. The SSD will connect to the Pi’s USB hub
  b. The cell kit will sit atop the Pi, connected through GP/IO interface
  c. The circuit board will connect through pins to the Pi, and the pins used are up to you (See appendix for Sixfab Cellular HAT pinout, and section 3.4 for more information).
  d. The Pi must be connected to power
  e. The cell kit should be powered separately through the micro-USB connector on the side.
4. Power up the Pi.
  a. The Green ACT light next to the red power light should flash lightly, indicating that the SSD is being read
    i. In case of failure to read from SSD, flash a version of the Raspbian OS onto SD Card (using Raspberry Pi Imager - open source and online) and insert the SD card into the Pi - this will bypass boot from USB. More information can be found here: Installing operating system images - Raspberry Pi Documentation (https://www.raspberrypi.org/documentation/installation/installing-images/)
  b. Connect through HDMI to a monitor to have access to command line and code within the Pi
  c. Connect a keyboard and mouse to the Pi using the USB hub
5. Run necessary code or scripts from the Pi
  a. You can create and run scripts from command line using Ubuntu commands
  b. Scripts can be scheduled to run using linux cron jobs (See section 3.4)
  c. In the future, SSH’ing into the Pi will allow for use without the HDMI port, in a process outlined here: https://www.raspberrypi.org/documentation/remote-access/ssh/

2.2 PCB Instructions

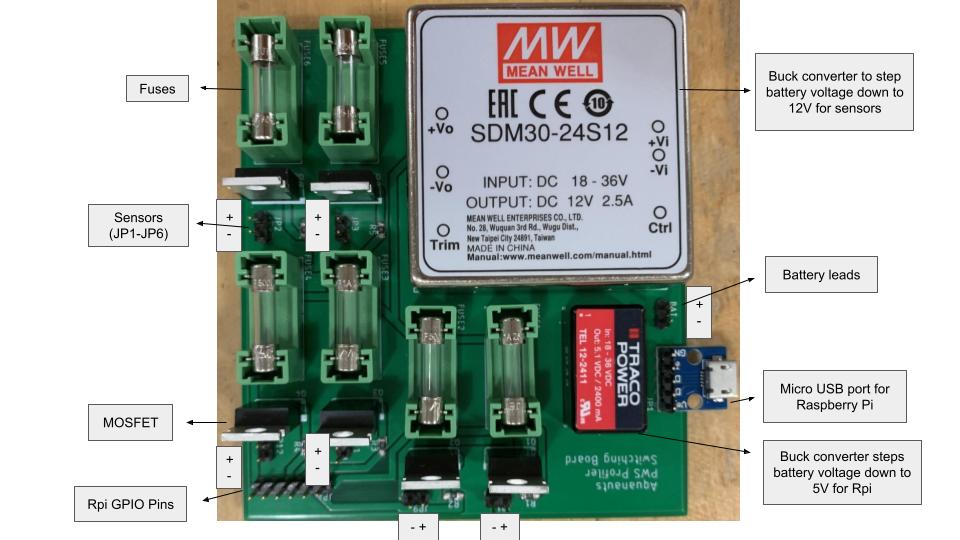
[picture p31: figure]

The figure above shows what all the components on the PCB are and their polarities for connecting parts.

1. Connect battery leads to the PCB following the polarity on the labeled figure above.
2. Use a micro USB to micro USB cable to connect the RPi to the PCB to receive power
3. Connect up to six sensors to their pin headers on the PCB. Ensure the positive and negative leads are attached following the labels on the above image.
4. Select RPi GPIO pins and connect them to the corresponding sensor’s pin on the pin header on the PCB.
3. How to Use

This section covers basic commands for sending files to a remote server with an FTP connection. The system originally designed by the Aquanauts uses the Sixfab cell kit with the Telit LE910C1-NF chip. However, it is recommended for the user to acquire a cell kit with the Quectel EC25EC21 chip in the future (discussed in section 3.3). The commands for sending data are similar and are discussed in their respective sections, 3.1 and 3.2. For more information on how to use Sixfabs hardware and software, visit the following link: https://docs.sixfab.com/.

3.1 Telit FTP Commands

The following commands can be used for sending a single file with the Telit module. See the references section for more details if this does not suit your needs [1].

1) AT+CGDCONT=<cid>,<PDP_type>,<APN>
- <cid> integer that sets the context ID, which can be 1-16
- <PDP_type> string that sets the Packet Data Protocol type can be one of the following:
- “IP” - IPv4
- “PPP” - Point to Point
- “IPv6” - IPv6
- <APN> string of the access point name
- This is usually the name or IP of the nearest cell tower
2) AT#PDPAUTH=<cid>,<auth_type>,<username>,<password>
- <cid> is an integer of the context ID 1-16
- <auth_type> is an integer that represents the authentication type:
- 0: no authentication (default)
- 1: PAP
- 2: CHAP
- <username> and <password> are strings of the credentials given to you by your internet provider (not needed for authentication type 0)
3) AT#GPRS=1
- GPRS context must be attached before opening an FTP connection
- 0 would deactivate this
4) AT+CGACT=<state>,<cid>
- <state> deactivates or activates the PDP context with 0 or 1, respectively
- <cid> is an integer of the context ID 1-16
5) AT#FTPOPEN=<server:port>,<username>,<password>,<mode>
- This command opens the FTP connection
- <server:port> is of type string
- The server can be in IPv4 or IPv6 format
- The port number is 21 by default
- <mode> can be 0 or 1, which are active or passive, respectively
- It is recommended to provide the port number and to use active mode
6) AT#FTPCFG=<tout>,<IPPignoring>,<FTPSEn>,<FTPext>
- <tout> is the time-out interval in 100 ms units (default is 100 ms and max is 5000 ms)
- <IPPignoring> disables or enables the use of the private IP sent by the server with 0 or 1, respectively
- It is recommended to set this to enable this to 1
- <FTPSEn> disables or enables FTPS for security with 0 or 1, respectively
- <FTPext> -- this is recommended to be set to 0 (see references for more details [1])
7) AT#FTPPUT=<filename>,<connMode>
- This command sends a file
- <filename> is a string, which can be no more than 200 characters long
- <connMode> can be 0 or 1, which are online or command, respectively
- It is recommended to set this to 0 for online mode
8) AT#FTPTYPE=<type>
- <type> sets the file transfer type to binary or ascii with 0 or 1, respectively
9) AT#FTPCLOSE
- This command closes the FTP connection

***Note: Please reference the following link for how to set up a connection to your local cellular network based on your carrier: Data Call – AT commands to set up GPRS/EDGE/UMTS/LTE data call | M2MSupport.net (https://m2msupport.net/m2msupport/data-call-at-commands-to-set-up-gprsedgeumtslte-data-call/)

3.2 Quectel FTP Commands

The following commands are all you need for sending a single file with the Quectel module. This walkthrough will strictly use FTP rather than FTPS. See the references for more details if this does not suit your needs, or if you would like to use FTPS instead [2][3][4].

1) AT+QICSGP=<contextID>,<context_type>,<APN>,<username>,<password>,<authentication>
- <contextID> integer from 1-16
- <contect_type> can be set to 1 or 2, which is IPv4 or IPv6, respectively
- <APN> string of the access point name
- This is usually the name or IP of the nearest cell tower
- <username> and <password> are strings of your cellular account credentials
- <authentication> integer to determine the authentication method
- 0: NONE
- 1: PAP
- 2: CHAP
- 3: PAP or CHAP
2) AT+QIACT=<contextID>
- Activates the context created in the last step
3) AT+QFTPCFG="contextid",<contextID>
- Configures and uses the context
4) AT+QFTPCFG="account",<username>,<password>
- <username> and <password> are strings used to log into the FTP server
5) AT+QFTPCFG="filetype",<filetype>
- <filetype> integer that determines the filetype:
- 0: binary
- 1: ascii
6) AT+QFTPCFG="transmode",<transmode>
- <transmode> integer that determines the filetype:
- 0: active mode (recommended for this project)
- 1: passive mode
7) AT+QFTPCFG="rsptimeout",<timeout>
- <timeout> integer that determines the timeout interval in seconds (can be 20-180)
8) AT+QFTPOPEN=<hostname>,<port>
- This command opens the connection to the FTP server
- <hostname> and <port> are both strings, and are related to the FTP server itself
9) AT+QFUPL=<filename>
- Uploads the desired file
10) AT+QFTPCLOSE
- Closes the connection

***Note: Please reference the following link for how to set up a connection to your local cellular network based on your carrier: Data Call – AT commands to set up GPRS/EDGE/UMTS/LTE data call | M2MSupport.net (https://m2msupport.net/m2msupport/data-call-at-commands-to-set-up-gprsedgeumtslte-data-call/)

3.3 Benefits to Using the Quectel Chip

It is recommended that the Sixfab Cellular Kit is specified with the Quectel EC25 chip. This is an option provided by Sixfab when purchasing the Sixfab 4G/LTE Cellular Kit. This is due to the fact that the Telit LE910C1-NF chip is not compatible with AT commands via UART, while the Quectel EC25 chip is compatible with AT commands via UART. The Sixfab Cellular Kit will require its own power source to avoid causing low power warnings from the Raspberry Pi, thus occupying the USB port on the cellular kit and eliminating the possibility of sending AT commands from the Raspberry Pi to the Sixfab Cellular HAT via USB.

3.4 Turning Sensors On and Off

To turn sensors on and off: (Note: all script examples are in Python syntax)

1) Individually connect each MOSFET on the PCB to any available GPIO pins on the Raspberry Pi. The only pins in use are GPIO14 (pin 8), GPIO15 (pin 10), GPIO6 (pin 31), GPIO13 (pin 33), GPIO19 (pin 35), and GPIO26 (pin 37) all occupied by the Sixfab Cellular HAT. Note: see the appendix for a pinout of the Sixfab Cellular HAT.
2) To set up pins for voltage output, use the following example:
  a) GPIO.setmode() accepts two parameters: GPIO.BCM, and GPIO.BOARD. GPIO.BCM will use GPIO numbering (GPIO23 is pin 23), while GPIO.BOARD will use board numbering (GPIO23 is pin 16).
  b) GPIO.setup defines whether the pin is an input pin or an output pin. For this use case, the pins will always be set up as output pins using the GPIO.OUT parameter. There needs to be one GPIO.setup command per pin. Example:

import RPi.GPIO as GPIO

GPIO.setmode(GPIO.BCM) #use BCM numbering

GPIO.setup(16, GPIO.OUT) #set up GPIO16 as output pin

3) To turn individual pins on and off:
  a) The GPIO.output() command accepts two parameters: a pin number, and 1 (high) or 0 (low). Example:

GPIO.output(16,1) #sets GPIO16 to high using BCM numbering

The information above can be used to formulate a script for turning individual pins on and off. Example script to set all pins high (all connected sensors ON):

import RPi.GPIO as GPIO

GPIO.setmode(GPIO.BCM) #use BCM numbering

GPIO.setup(23, GPIO.OUT) #set up GPIO23 as output pin

GPIO.setup(24, GPIO.OUT)

GPIO.setup(25, GPIO.OUT)

GPIO.setup(17, GPIO.OUT)

GPIO.setup(22, GPIO.OUT)

GPIO.setup(27, GPIO.OUT)

GPIO.output(23,1) #set GPIO23 high

GPIO.output(24,1)

GPIO.output(25,1)

GPIO.output(17,1)

GPIO.output(22,1)

GPIO.output(27,1)

Example script to set all pins low (all connected sensors OFF):

import RPi.GPIO as GPIO

GPIO.setmode(GPIO.BCM) #use BCM numbering

GPIO.setup(23, GPIO.OUT) #set up GPIO23 as output pin

GPIO.setup(24, GPIO.OUT)

GPIO.setup(25, GPIO.OUT)

GPIO.setup(17, GPIO.OUT)

GPIO.setup(22, GPIO.OUT)

GPIO.setup(27, GPIO.OUT)

GPIO.output(23,0) #set GPIO23 low

GPIO.output(24,0)

GPIO.output(25,0)

GPIO.output(17,0)

GPIO.output(22,0)

GPIO.output(27,0)

4) To schedule this automatically, the simplest and most straightforward method is to execute your script inside of a cron job. A cron job is an automated task that will execute regularly on a defined schedule. More information about cron jobs can be found at the following link:

How To Schedule Python Scripts As Cron Jobs With Crontab (Mac/Linux) | Python Engineer (python-engineer.com) (https://www.python-engineer.com/posts/cron-jobs-for-python/)

4. Monitoring the Sixfab Cell Kit

Sixfab offers an easy to use interface to interact with the SIM card of the device. This can be located here: https://connect.sixfab.com/#/auth/login. The current login is associated with a student’s e-mail and information, where the login information is:

ID: 4873_project

Password: drwestiscool

On this site, the usage can be monitored, billing occurs for the SIM card, and you can perform remote maintenance on the SIM card. The instructions are easy to follow and provide an ease of access that’s unmatched. For more information, visit the following link: https://docs.sixfab.com/docs/sixfab-core-introduction.

5. References
1. Telit_LE910Cx_AT_Commands_Reference_Guide_r8.pdf. Accessible online at: https://sixfab.com/wp-content/uploads/2020/08/Telit_LE910Cx_AT_Commands_Reference_Guide_r8.pdf.
2. QuectelEC2x26EG9x26EM05FTPSATCommandsManualV10.116697075.pdf. Accessible online at: https://usermanual.wiki/Document/QuectelEC2x26EG9x26EM05FTPSATCommandsManualV10.116697075/view.
3. Quectel_EC2xEG9xEM05_TCPIP_AT_Commands_Manual_V1.0.pdf. Accessible online at: https://sixfab.com/wp-content/uploads/2018/09/Quectel_EC2xEG9xEM05_TCPIP_AT_Commands_Manual_V1.0.pdf.
4. Quectel_EC20_FILE_AT_Commands_Manual.pdf. Accessible online at: https://www.cika.com/soporte/Information/GSMmodules/Quectel/EC20/Quectel_EC20_FILE_AT_Commands_Manual.pdf.

Appendix

Sensors | Min Voltage | Max Voltage | Min Current (mA) | Max Current (mA)
SBE 16plus V2 | 9 | 28 | N/A | N/A
SBE 43 | 6.5 | 24 | 2.5 | 9.23
SUNA Nitrate Sensor | 8 | 18 | 416.67 | 937.5
Echo Fluorometer | 7 | 15 | 60 | 140

Sixfab Cellular HAT Pinout

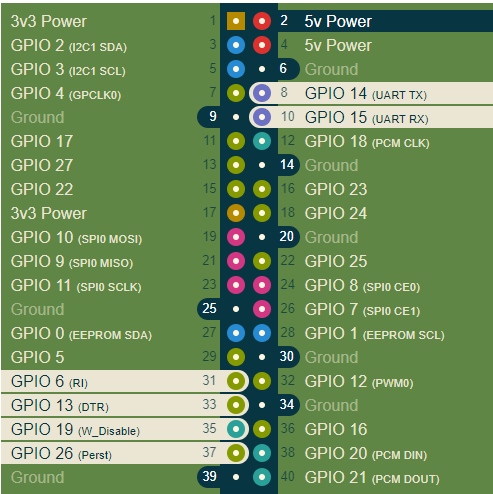
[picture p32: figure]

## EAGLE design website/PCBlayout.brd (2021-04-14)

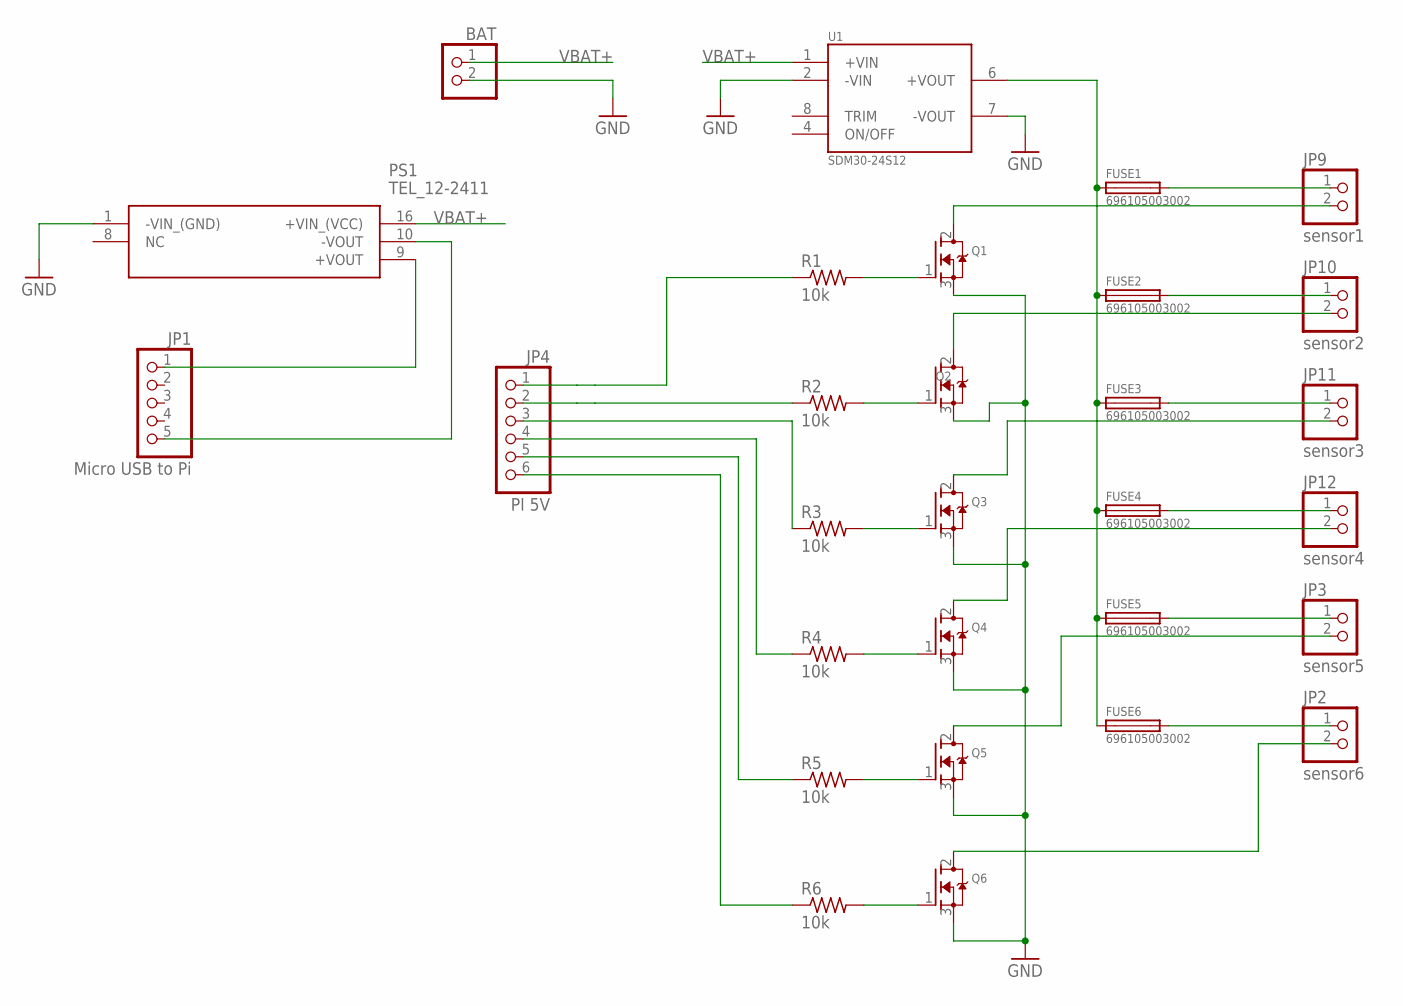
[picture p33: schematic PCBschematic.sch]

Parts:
BAT: PINHD-1X2; 1X02
FUSE1, FUSE2, FUSE3, FUSE4, FUSE5, FUSE6: 696105003002; FUSE_696105003002
JP1: Micro USB to Pi; 1X05
JP2: sensor6; 1X02
JP3: sensor5; 1X02
JP4: PI 5V; 1X06
JP9: sensor1; 1X02
JP10: sensor2; 1X02
JP11: sensor3; 1X02
JP12: sensor4; 1X02
PS1: TEL_12-2411; TEL122411
Q1, Q2, Q3, Q4, Q5, Q6: MOSFET-NGDS_TO220V; TO220V
R1, R2, R3, R4, R5, R6: 10k; M0805
U1: SDM30-24S12; CONV_SDM30-24S12

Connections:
GND: BAT.2, PS1.1 (-VIN_(GND)), Q1.3 (S), Q2.3 (S), Q3.3 (S), Q4.3 (S), Q5.3 (S), Q6.3 (S), U1.2 (-VIN), U1.7 (-VOUT)
unnamed: JP1.1, PS1.9 (+VOUT)
unnamed: JP1.5, PS1.10 (-VOUT)
unnamed: FUSE1.2, JP9.1
unnamed: FUSE2.2, JP10.1
unnamed: FUSE3.2, JP11.1
unnamed: FUSE4.2, JP12.1
unnamed: FUSE1.1, FUSE2.1, FUSE3.1, FUSE4.1, FUSE5.1, FUSE6.1, U1.6 (+VOUT)
unnamed: JP9.2, Q1.2 (D)
unnamed: JP10.2, Q2.2 (D)
unnamed: JP11.2, Q3.2 (D)
unnamed: JP12.2, Q4.2 (D)
unnamed: Q1.1 (G), R1.2
unnamed: Q2.1 (G), R2.2
unnamed: Q3.1 (G), R3.2
unnamed: Q4.1 (G), R4.2
unnamed: JP4.1, R1.1
unnamed: JP4.2, R2.1
unnamed: JP4.3, R3.1
unnamed: JP4.4, R4.1
unnamed: FUSE6.2, JP2.1
unnamed: JP2.2, Q6.2 (D)
unnamed: Q5.1 (G), R5.2
unnamed: Q6.1 (G), R6.2
unnamed: JP4.5, R5.1
unnamed: JP4.6, R6.1
unnamed: FUSE5.2, JP3.1
unnamed: JP3.2, Q5.2 (D)
VBAT+: BAT.1, PS1.16 (+VIN_(VCC)), U1.1 (+VIN)

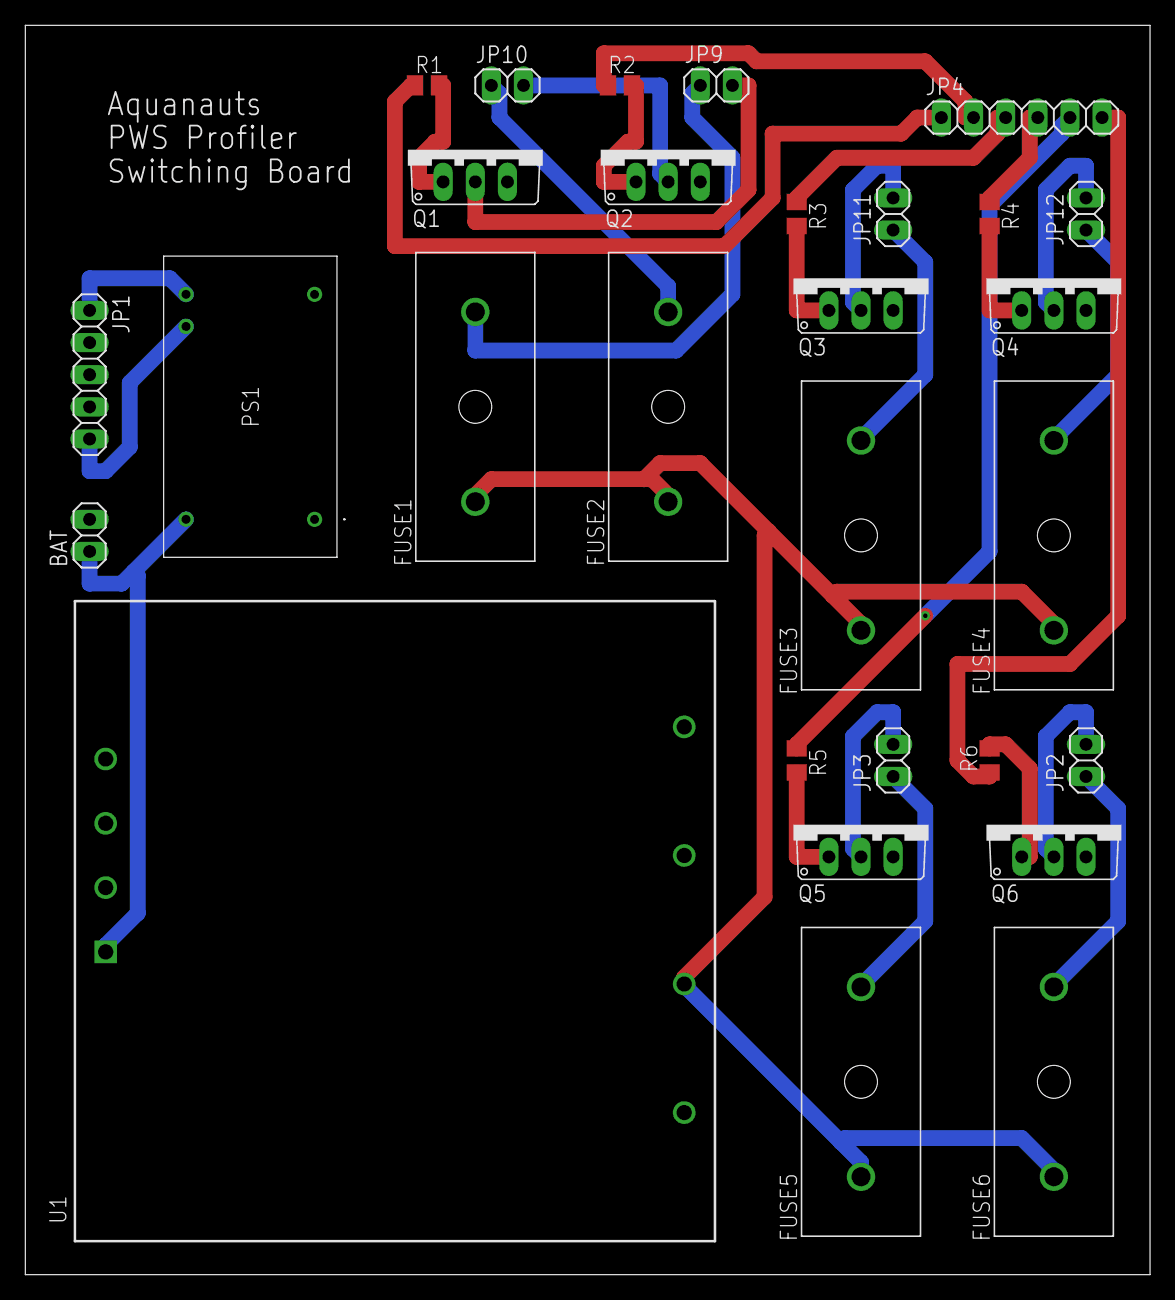
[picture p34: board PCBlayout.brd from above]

Board: 2 copper layers, 88.9 x 98.7 mm, 29 parts (0 on the bottom side), 29 nets.

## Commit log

2021-04-08 Added comms diagram, power diagram, and GitHub link to website under section called Additional Supporting Documentation
2021-04-09 Updated power diagram
2021-04-14 Added schematic and board files for the PCB
    [PCBlayout.brd, PCBschematic.sch]
